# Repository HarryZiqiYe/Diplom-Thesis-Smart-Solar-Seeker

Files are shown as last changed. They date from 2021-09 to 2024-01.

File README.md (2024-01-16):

# Smart-Solar-Seeker

### Abstract

The paper hand in deals with the tracking of the sun, which follows the position of the sun, to get the maximum efficiency. Solar technology is a renewable energy source, that contributes to a sustainable environment. In contrast to flat lying solar panels, it is possible to produce more energy through tracking. A prototype has been developed and constructed which performs mostly all our tasks that we need.

Most of the mechanical components are standard aluminum profiles which are mainly used for the framework of our system, which can withstand weather and physical influences.
Furthermore, the project covers the implementation of a control algorithm on a microcontroller.
An GPS unit and light sensors have been used, which represents the input data of our algorithm. Two actuators, which have been installed, are controlled by the algorithm which are supposed to bring the solar panel to the the best solar radiation. The group compares with the measurements taken how economical it is to track and if it is necessary to rotate on two axes. An ESP32 microcontroller is used in the project and programmed with C++. Some circuit boards have been designed and implanted for our regulation of the supply voltage and for control of actuators, which uses inductors, relays, resistors, and other specific electronical components.

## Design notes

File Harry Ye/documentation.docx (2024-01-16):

# Photovoltaik: Stromerzeugung durch Sonnenenergie

Die Photovoltaik ist ein Prozess, bei der die Lichtenergie mit Hilfe von Solarzellen direkt in elektrische Energie umgewandelt wird. Diese Form der Energieerzeugung zählt zu den erneuerbaren.

# 1.1. Photoelektrischer Effekt

Unter den photoelektrischen Effekt (Photoeffekt oder lichtelektrischen Effekt) versteht man die Wechselwirkung der Elektronen mit den Photonen des Lichtes. Dabei nehmen die Elektronen die Photonen auf besser gesagt ihre Energie und lösen sich aus der Bindung des jeweiligen Stoffes. Diese Energie kann mit der Formel

| E=h∙f | (1.1)

E…Energie

h…Planck’sches Wirkungsquantum

f…Frequenz

berechnen. Um sich herauslösen zu können, muss die Photonenenergie größer als die Bindungsenergie des Elektrons sein. Es gibt drei Arten des photoelektrischen Effekts: äußeren, inneren und Photoionisation, wobei auf den inneren photoelektrischen Effekt genauer eingegangen wird.[1]

# 1.1.1. Äußerer photoelektrischer Effekt

Dieser Effekt wird auch als Photoemission oder Hallwachs-Effekt bezeichnet. Er beschreibt das Herauslösen der Elektronen aus einem Halbleiter- oder Metalloberfläche, wenn sie mit Licht bestrahlt wird. Dazu muss die Photonenenergie größer als die Austrittsarbeit des Materials sein. Mit der Gegenfeldmethode kann der Effekt demonstriert und die Austrittsarbeit bestimmt werden.

Abbildung 1.1 veranschaulicht dieses Phänomen.[2]

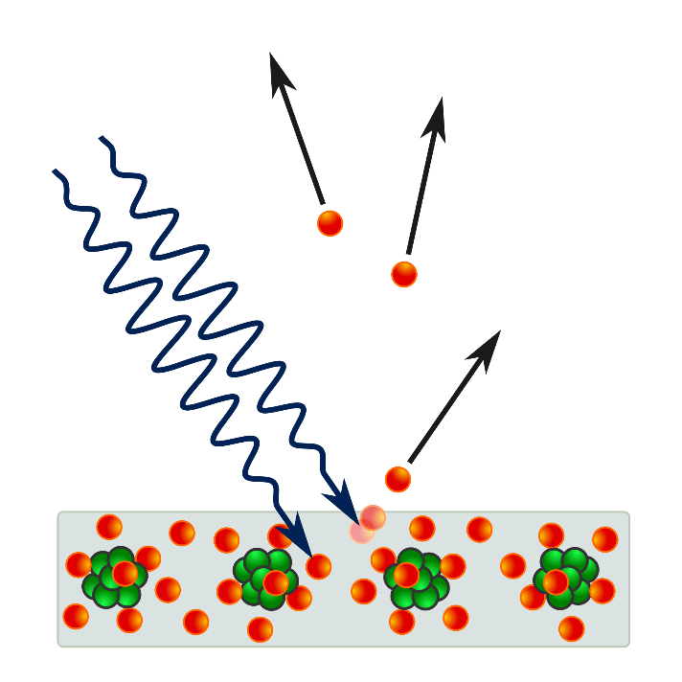
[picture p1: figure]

Abbildung 1.1: Äußerer photoelektrischer Effekt

# 1.1.2. Innerer photoelektrischer Effekt

Dieser Effekt tritt ausschließlich in Halbleiter auf. Zwei Fälle beschreiben diesen Effekt: Photoleitung und photovoltaischer Effekt.

# 1.1.2.1. Photoleitung

Wenn durch die Lichtbestrahlung die Leitfähigkeit eine Halbmaterials erhöht wird, spricht man von der Photoleitung. Um diesen Effekt besser verstehen zu können, ist das Bändermodell (Abbildung 1.2) abgebildet.

Abbildung 1.2: Bändermodell

Aufgrund der aufgebrachten Photonenenergie werden die Elektronen vom Valenzband in das Leitungsband gehoben. Die Photonen müssen so viel Energie aufbringen, bis die Elektronen die Bandlücke bzw. verbotenen Zone überwinden können. Während dieses Prozesses hinterlässt das Elektron ein Loch im Valenzband. So kommt es zur Bildung eines Elektronen-Loch Paars. Das Elektron im Leitungsband ist nun frei beweglich.[3]

# 1.1.2.2. Photovoltaischer Effekt

Durch das Prinzip der Photoleitung kann mit einem Halbleiter Licht in elektrische Energie umgewandelt werden. Dazu wird die Funktion einer Diode und seiner Raumladungszone gebraucht. Die Photonen brechen die Elektronenpaarbindungen auf. Wenn ein Verbraucher angeschlossen wird, ziehen sich die freibeweglichen Teilchen an und ein Strom beginnt zu fließen. Abbildung 1.3 stellt den Aufbau und die Funktion einer Solarzelle dar.[4]

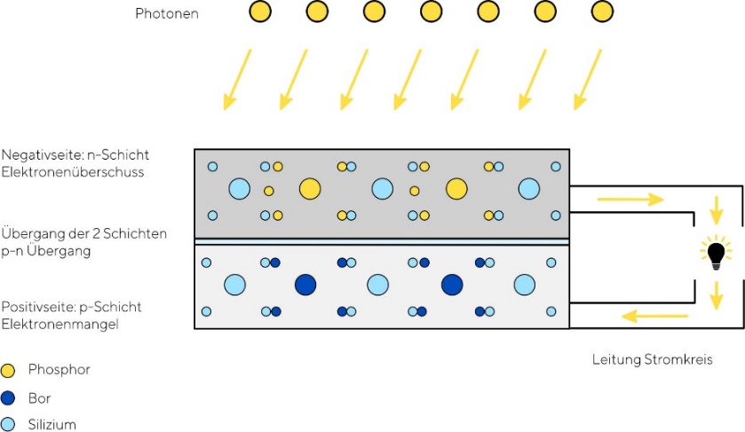
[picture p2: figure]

Abbildung 1.3: Solarzelle

# 1.2. Silizium-Solarzelle

Eine Solarzelle wandelt auf Grund des photovoltaischen Effektes Sonnenlicht in elektrische Energie um. Sie besteht aus einem Halbleitermaterial, wie Galliumarsenid, Cadmiumtellurid oder Chalkopyrite. Jedoch ist Silizium das häufigste verwendete Halbleitermaterial, weil es in großen Mengen zur Verfügung steht. Silizium-Solarzellen unterscheiden sich in zwei Arten: dickschichtig und dünnschichtig. Zu den Dickschichtzellen zählen die monokristallinen und polykristallinen Zellen und die amorphe Zelle gehört zu den Dünnschichtzellen.

# 1.2.1. Herstellung

Als Erstes wird aus Quarzsand Silizium gewonnen. Das Silizium wird zu Ingots verarbeitet. Danach werden die Ingots durch das Sägen zu Wafer. Die Wafer werden zu Solarzellen verbaut. (Abbildung 1.4)

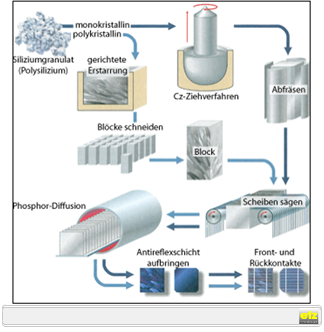
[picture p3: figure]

Abbildung 1.4: Herstellung

# 1.2.2. Verschiedene Typen von Solarzellen

Monokristallin: Solche Solarzellen bestehen aus einkristallinem Silizium, weshalb der Siliziumanteil sehr hoch ist. Der Wirkungsgrad einer monokristalline Zelle liegt bei ca. 20%. Sie ist vergleichsweise teurer als die anderen wegen der aufwendigeren Produktion.

Polykristallin: Bei den polykristalline Zellen ist das Silizium nicht so rein. Dadurch ist die Produktion weniger aufwendig und der Preis ist billiger, weshalb polykristalline Zellen das beste Preis-Leistung-Verhältnis haben. Der Wirkungsgrad liegt bei 15%.

Amorph: Dünnschichtzellen sind nichtkristallin. Das heißt, dass das Silizium mit anderen Materialien vermischt wird und auf eine dünne Schicht aufgetragen wird. Deshalb ist der Wirkungsgrad nur zwischen 5-7%. Jedoch sind sie flexibel und lassen sich falten und rollen. Die Zellen sind günstiger als Dickschichtzellen.[5]

# 1.2.3. Technische Merkmale

# 1.2.3.1. Kenngrößen

In den üblichen Technischen Datenblätter stehen folgende Kennwerte:

- ISC: Kurzschlussstrom
- VOC: Leerlaufspannung
- VMPP: Spannung bei maximaler Leistung
- IMPP: Strom bei maximaler Leistung
- PMPP: Maximale erzielbare Leistung unter STC
- FF: Füllfaktor

Der Füllfaktor ist ein Verhältnis zwischen der Leistung PMPP (Blau) und dem Produkt von ISC und VOC (Gelb) und dementsprechend dimensionslos. Sie gibt die Qualität der Zelle an. Für einen höheren Wirkungsgrad muss der Füllfaktor auch höher sein.

Abbildung 1.5: Füllfaktor

Den Füllfaktor berechnet man sich mit dieser Formel:

| FF=(P_(MPP))/(U_(OC) ∙I_(SC)) | (1.2)

PMPP … maximale Leistung

UOC … Leerlaufspannung

ISC … Kurzschlussstrom

TK PMPP: Koeffizient für die Leistungsänderung abhängig von der Zellentemperatur.

η: Zellwirkungsgrad

| η=(P_(MPP))/(A∙E_e) | (1.3)

A … bestrahlte Fläche

Ee … Bestrahlungsstärke

Aus den Kennwerten kann eine Strom-Spannungs-Kennlinie erstellt werden (Abbildung 1.6).[6]

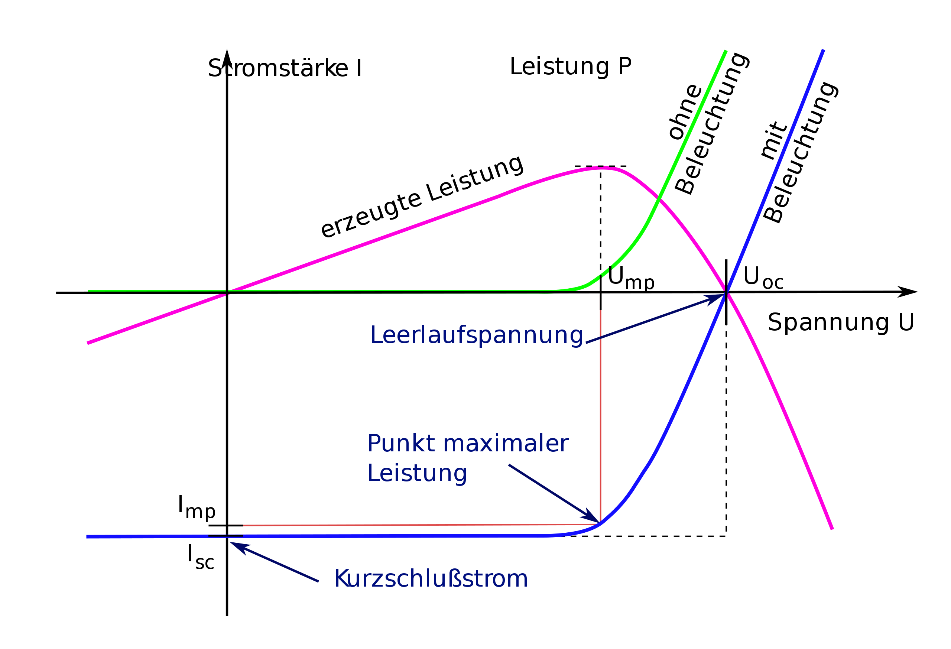
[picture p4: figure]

Abbildung 1.6: Strom-Spannungs-Kennlinie

# 1.2.3.2. Schaltbilder

Das Schaltsymbol einer Solarzelle (Abbildung 1.7).

Abbildung 1.7: Schaltsymbol

Ein Ersatzschaltbild schaut folgendermaßen aus (Abbildung 1.8):

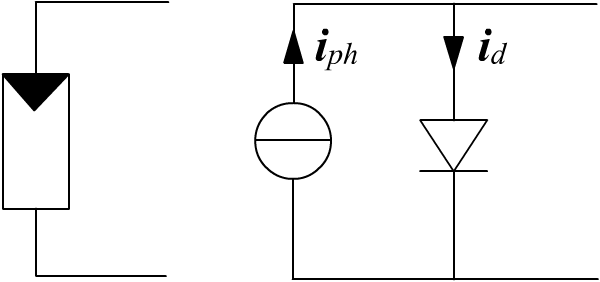
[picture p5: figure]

Abbildung 1.8: Ersatzschaltbild

Links ist das Schaltzeichen einer Solarzelle und Rechts abgebildet ihr Ersatzschaltbild. Die Gesamtstromstärke wird errechnet mit:[7]

| I=I_(ph) -I_D | (1.4)

# 1.2.4. Solarpanel

Einzelne Solarzellen werden in Reihe bzw. in Serie geschalten (Abbildung 1.9). Dadurch entsteht ein Solarpanel oder Solarmodul. Die Spannungen der jeweiligen Solarzelle werden zusammenaddiert. Werden die Solarzellen parallel geschalten, so werden die Ströme addiert (1.10).

Abbildung 1.9: Reihenschaltung

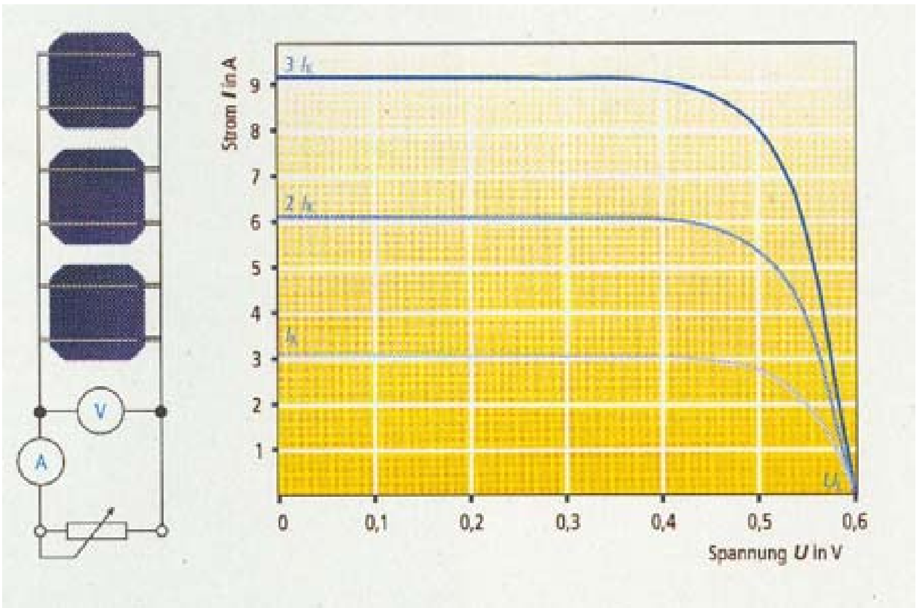
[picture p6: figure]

Abbildung 1.10: Parallelschaltung

Häufig befinden sich Bypass-Dioden bzw. Freilaufdioden in den Solarmodulen. Abbildung 1.11 zeigt eine abgeschattete Solarzelle in einer Reihenschaltung.

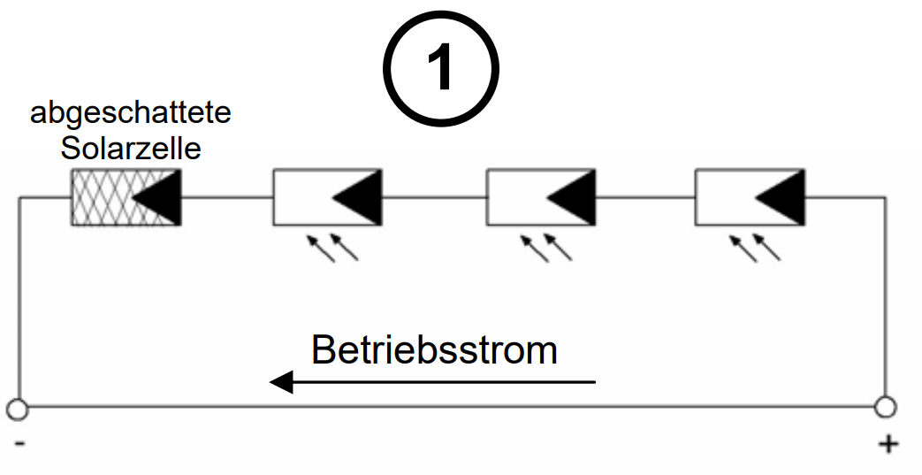
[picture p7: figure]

Abbildung 1.11: abgeschattete Solarzelle

Diese abgeschattete Zelle wirkt wie ein Widerstand bzw. Verbraucher. Der durchfließende Strom wandelt sich in Wärme um und die Solarzelle überhitzt sich. Das wird Hotspot genannt (Abbildung 1.12).

Abbildung 1.12: Hotspot

Wird nun eine Freilaufdiode antiparallel geschaltet, entsteht ein Kurzschluss und die Diode leitet den Strom um (Abbildung 1.13).

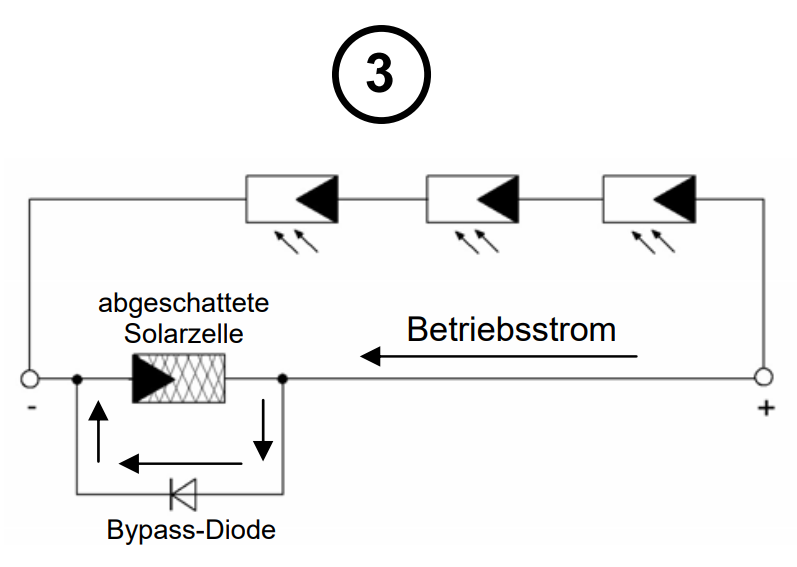
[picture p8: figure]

Abbildung 1.13: Bypass-Diode

In der Praxis wird nur eine Bypass-Diode pro Solarmodul verbaut. Das heißt ist ein Solarmodul beschattet, so leitet die Diode den Strom um (Abbildung 1.14).[8]

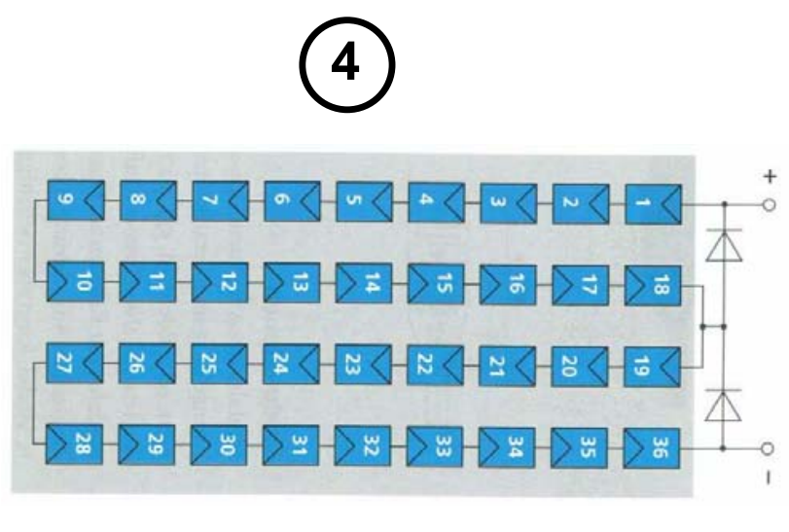
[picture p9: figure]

Abbildung 1.14: eine Bypass-Diode pro Solarmodul

In unserem Projekt wird ein monokristallines Solarpanel verwendet. Technische Daten:

- Nennleistung Pmax: 90W mit einer Toleranz von 5%
- Strom bei Pmax Imp: 5,25A
- Spannung bei Pmax Vmp: 17,98V
- Kurschlussstrom ISC: 5,65A
- Leerlaufspannung VOC: 22,77V
- Gewicht: 7,8kg
- Abmessungen: 1185x545x35mm

# 1.2.5. Wirkungsgrad

Der Wirkungsgrad ist das Verhältnis der Ausgangsgröße und die Eingangsgröße. Beim Leistungsverhältnis einer Solarzelle ist es die erzeugte elektrische Leistung durch die einfallende Strahlung:

| η=(P_(elektrisch))/(P_(Licht)) | (1.5)

η … Wirkungsgrad

Pelektrisch … erzeugte elektrische Leistung

PLicht … einfallende Strahlungsleistung

Wirkungsgrade der verschiedenen Zellarten:

Material | Max. Wirkungsgrad im Labor | Max. Wirkungsgrad Serienproduktion | Typ. Wirkungsgrad Serienproduktion | Flächenbedarf pro kW
Monokristallin | 26,1% | 24% | 19% | 5,3m²
Polykristallin | 22,3% | 20% | 17% | 5,9m²
Amorph | 14% | 8% | 6% | 16,7m²

Der Wirkungsgrad der Solarzellen wird mit den Standard-Test-Conditions gemessen (1000 Watt Lichteinstrahlung, 25 Grad Zelltemperatur, Air Mass von 1,5).

Um den Wirkungsgrad einer Solarzelle technisch zu verbessern, muss das Material mehr Lichtwellen des Spektrums verarbeiten können. Tandem-Solarzellen bestehen aus verschiedenen Stapeln von Materialien, somit wird ein breiteres Spektrum abgedeckt.[9]

Eine Solarzelle kann auch Wirkungsgrad verlieren. Wenn die Zelltemperatur zu hoch ist, verliert die Zelle an Wirkungsgrad, weil sie weniger Leistung erzeugt. In der Regel nach den STCs sinkt die Leistung um 0,4% pro Grad Celsius. Außerdem haben Solarzellen eine bestimmte Lebensdauer. Bei kristallinen Zellen liegen sie über 30 Jahren und bei amorphen 20 bis 25 Jahren. Von Jahr zu Jahr verringert sich der Wirkungsgrad einer Solarzelle.[10]

# 1.3. Azimut und Elevation

Azimut und Elevation sind Maße, die die Koordinaten eines Objektes in der Atmosphäre beschreibt. Die Richtung gibt der Azimut an und die Höhe die Elevation. Beide werden in Grad angegeben. Abbildung 1.15 zeigt einen Satellit und seiner Elevation und seines Azimuts. Auch der Standort der Sonne kann mit den beiden Größen bestimmt werden.

Abbildung 1.15: Azimut und Elevation

Der Winkel zwischen Meridian und des Satelliten ist der Azimut. Von Norden im Uhrzeigersinn wird gemessen. Eine volle Umdrehung ist 360°.

Der Winkel zwischen dem Horizont und des Mittelpunktes wird Elevation genannt. Im Zenit ist der maximale Elevationswinkel 90°.[11]

# Regelungsentwickelung

# 1.4. Recherche und Vorwissen

Regeln ist das selbsttätige Beeinflussen eines technischen Prozesses (einer Anlage, eines Systems) in gezielter Weise. Dabei handelt es sich um einen geschlossenen Wirkungsablauf; das heißt, die den Prozess beeinflussenden Größen werden mit geeigneten Regeleinrichtungen aus gemessenen Prozessgrößen selbst gebildet und nicht nur von außen vorgegeben.[^1]

Abbildung 2.1 veranschaulicht die Regelung einer antiken Wasseruhr.

Abbildung 2.1: Antike Wasseruhr

Bei einer bestimmten Füllhöhe h des Wassers sind der Zufluss und Abfluss gleichgroß ( q_z =q_a ), weil der Schwimmer den Zufluss bei steigender Wasserhöhe verringert.[12]

# 1.4.1. Darstellung eines Regelungssystems

Ein Geräteplan stellt schematisch die gerätemäßige Realisierung einer Regelung dar (Abbildung 2.2).

Abbildung 2.2: Geräteplan

Die Drehzahl des Motors wird gemessen. Anhand des Istwertes wird eine entsprechende Steuerspannung in den Stromrichter geschickt, um den Sollwert anzunähern.

Ein Blockschaltbild stellt die Regelung in Funktionsblöcken dar. Dabei werden die einzelnen Funktionen der Geräte vereinfacht. Abbildung 2.3 zeigt die obige Drehzahlregelung als vereinfachtes Blockschaltbild an.[12]

Abbildung 2.3: Blockschaltbild

# 1.4.2. Regelkreis

Die Abbildung 2.3 zeigt den Aufbau eines Regelkreises. Allgemein schaut der Regelkreis so aus:

Abbildung 2.4: Regelkreis

Elemente:

- Regler: Der Regler versucht die Regelabweichung (Differenz zwischen Sollwert und Istwert) zu eliminieren bzw. auf null zu setzen. Dafür erzeugt er ein entsprechendes Signal.
- Stellglied: Dieses Signal nimmt das Stellglied (z.B. Verstärker, Stromrichter, Servomotor, Ventil) auf. Da das Signal des Reglers eine leistungsschwache Größe ist und die Regelstrecke meist eine leistungsstarke Größe benötigt, dafür wird ein Stellglied eingesetzt, das so eine Stellgröße ausgeben kann.
- Regelstrecke: Die Regelstrecke ist das System, das geregelt wird. Sie gibt die Regelgröße bzw. den Istwert aus.
- Messglied: Das Messglied misst den jetzigen Istwert. Dieser Istwert wird in eine für den Regler verwendbare Größe umgeformt.
- Störgröße: Da Störungen unvermeidlich sind, müssen sie so weit minimalisiert werden, bis sie irrelevant sind. Sie treten während der Regelung der Strecke auf.

Sehr oft wird der Regler und das Stellglied als einen Block zusammengefasst. Das gilt auch für die Regelstrecke und das Messglied. Daraus ergibt sich der Standardregelkreis (Abbildung 2.5):[12]

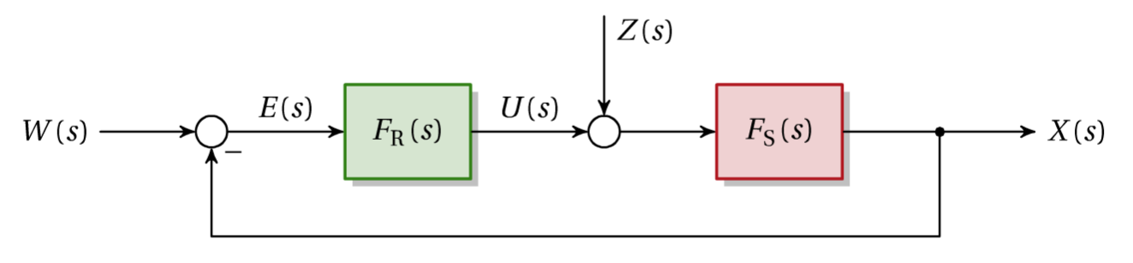
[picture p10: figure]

Abbildung 2.5: Standardregelkreis

Die wichtigsten Größen sind:

- X(s) … Regelgröße (Istwert)
- W(s) … Führungsgröße (Sollwert)
- E(s) … Regelabweichung
- U(s) … Stellgröße
- Z(s) … Störgröße
- FR(s) … Übertragungsfunktion des Reglers
- FS(s) … Übertragungsfunktion der Regelstrecke

Ohne der Rückführung im Regelkreis erhält man den offenen Regelkreis, mit der Übertragungsfunktion FO:[12]

| F_O (s)=F_R (s)∙F_S (s) | (2.1)

Schließt man den Regelkreises, bekommt man die Führungsübertragungsfunktion FW:

| F_W =(F_R ∙F_S)/(1+F_R ∙F_S)=(F_O)/(1+F_O) | (2.2)

# 1.4.3. Regler

Der Regler hat die Aufgabe, die Führungsgröße (Sollwert) mit der Regelgröße (Istwert) zu vergleichen und aus der Differenz beider Größen (Regelabweichung) eine entsprechende Stellgröße zu erzeugen.[^2] Zwischen den elektrischen Reglern unterscheidet man analoge und digitale.[12]

Es gibt drei Grundtypen der analogen Regler:

- P-Regler: Erzeugt eine der Regelabweichung proportionale Stellgröße. Vorteil: Schnelles Reagieren auf Regelabweichung, Nachteil: Regelt nie komplett aus (Ausnahme: Regelstrecke mit I-Anteil)
- I-Regler: Erzeugt eine Stellgröße, die dem zeitlichen Integral der Regelabweichung proportional ist. Vorteil: Genaue Regelung der Abweichung, Nachteil: Langsames Reagieren auf Regelabweichungen
- D-Regler: Erzeugt eine Stellgröße, die der momentane Änderungsrate der Regelabweichung proportional ist. Vorteil: Verbessert das Stabilitätsverhalten des Regelkreises, Nachteil: Regelt nicht aus → nur mit anderen Reglern sinnvoll

Durch Parallelschalten der einzelnen Grundregler erhält man:

- PI-Regler
- PD-Regler
- PID-Regler

Die Aspekte der einzelnen Regler werden kombiniert. Abbildung 2.6 veranschaulicht die Funktionen der Regler (Stellgrößen bei gegebener Regelabweichung):[12]

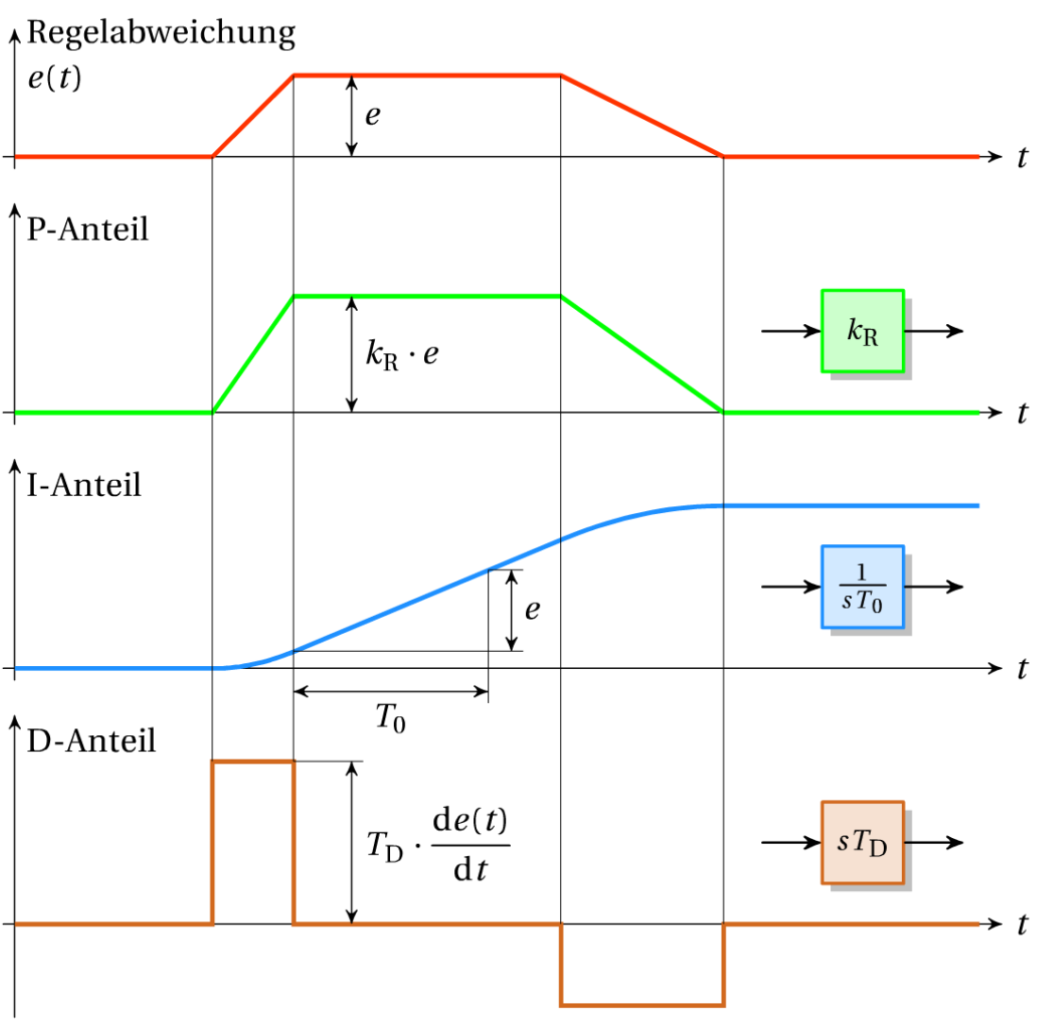
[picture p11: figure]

Abbildung 2.6: Erzeugte Stellgröße

Verglichen zu analoge Regler, die aus elektronische Bauteile (z.B. OPV) bestehen, werden für digitale Regler Computer (z.B. Mikrocontroller) verwendet. Die Regelgröße wird in periodischen Zeitabständen von einem Analog-Digital-Converter kurz ADC in eine digitale Größe konvertiert und vom Rechner eingelesen. Die Führungsgröße wird im Programm eingegeben oder von außen durch einen ADC hineingeschickt.[12]

Abbildung 2.7: Digitaler Regler

Im gespeicherten Programm des Computers arbeitet ein Regelalgorithmus Schritte ab, um die Stellgröße mit der berechneten Regelabweichung zu erhalten. Die Stellgröße kann entweder wieder in ein analoges Signal umgewandelt werden oder durch ein PWM-Signal gesendet werden.

Ein Digital-Analog-Converter wandelt digitale Signal in analoge um. Abbildung 2.8 veranschaulicht die analoge Umwandelung der Stellgröße.[12]

Abbildung 2.8: Analoge Umwandelung

Pro Zeitabstand wird die Stellgröße einmal abgetastet und bis zur nächsten Abtastung wird der Wert konstant gehalten.

Das pulsbreitenmodulierte Signal PWM stellt die Stellgröße als Rechtecksignal mit einer bestimmten Frequenz dar. Das Verhältnis zwischen der Impulsdauer und der Periodendauer, auch Duty-Cycle genannt, ermöglicht das Erzeugen eines bestimmten Stellgrößenwertes (Abbildung 2.9).

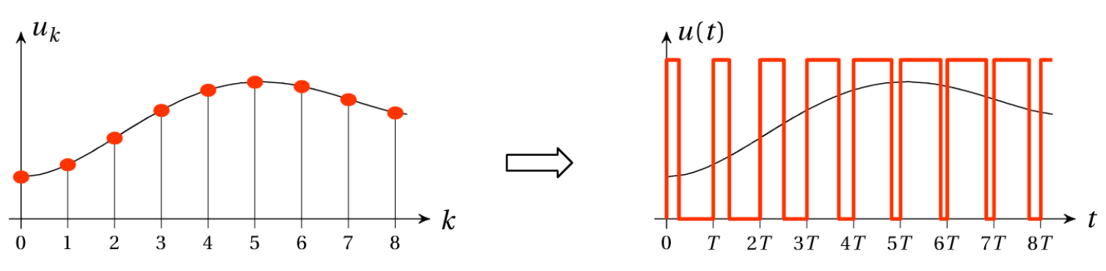
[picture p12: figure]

Abbildung 2.9: PWM

Da die Erzeugung des PWM-Signals rein softwaretechnisch verläuft, ist ein DAC nicht essenziell.[12]

# 1.4.4. Theoretischer Ansatz

Das Solarpanel wird zwei-achsig nachgeregelt. Ein Motor für die Azimut-Achse und ein anderes für die Elevation. Dabei wird zwischen Osten und Westen geregelt und danach der Höhenwinkel eingestellt. Nach der ersten Regelung wird jede Stunde wieder nachgeregelt. Bei schlechtem Wetter wie bei Bewölkung wird nicht nachgeregelt. Am Anfang der Regelung muss ein Nullpunkt definiert werden, damit das Programm richtig funktioniert.

# 1.4.5. Praktischer Ansatz

Abbildung 2.10 zeigt den entworfenen Regelkreis.

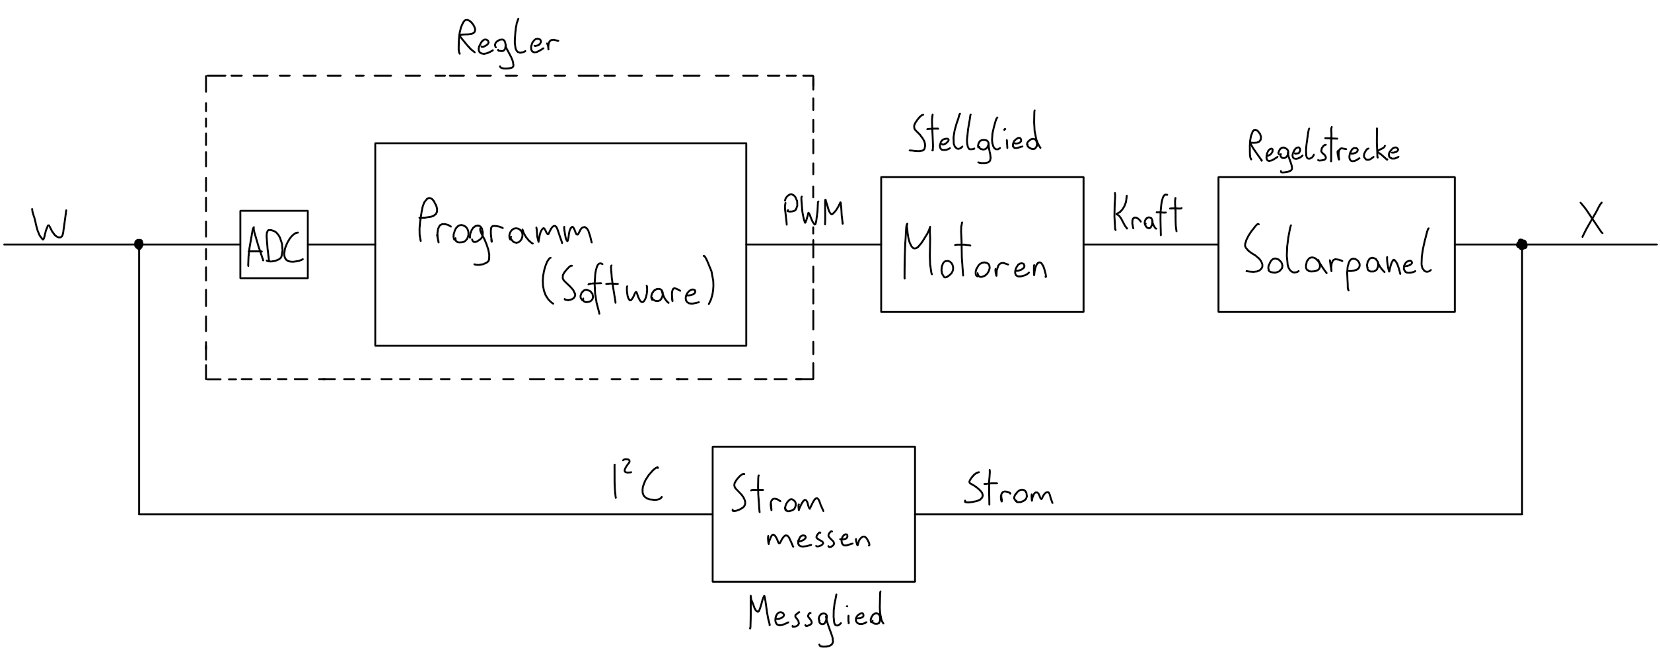
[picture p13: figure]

Abbildung 2.10: Theoretischer Ansatz

Für den digitalen Regler wird ein ESP32 verwendet, der alle benötigten Funktionen (Eingebauter ADC, I²C-Schnittstelle, das Erzeugen von PWM-Signalen, usw.) abdeckt (Regler). Das Bewegen des Azimuts beim Solarpanel erledigt ein Schrittmotor und beim Höhenwinkel ein Linearmotor (Stellglied). Im Gegensatz zum großem Solarpanel wird ein kleineres zur Messung des Stroms genommen (Regelstrecke). Das Messen übernimmt ein Stromsensor, der den Stromwert in digitale Spannungsimpulsen umwandelt und über die I²C-Schnittstelle zum Mikrokontroller schickt (Messglied). Im Folgenden werden die für die Regelung verwendeten Komponenten beschrieben.

# 1.5. Stromsensor

Der Stromsensor soll den Strom des kleineren Solarpanels messen und in eine digitale Größe umwandeln, damit der Mikrokontroller den Wert verarbeiten kann. Dabei werden zwischen zwei Arten unterschieden.

# 1.5.1. ACS712: Hall-Sensor

Die erste Variante der Strommessung ist mit einem Hallsensor. Er misst den Strom auf Basis des Halleffekts und wandelt ihn Spannung um. (Abbildung 2.11)

Abbildung 2.11: ACS712

# 1.5.1.1. Halleffekt

Wird ein stromdurchflossener Leiter in der Nähe eines Dauermagnets platziert, so bewegen sich die Ladungsträger senkrecht zum Magnetfeld des Dauermagnets, wodurch sich die geradlinigen Bahnen des Leiters krümmen. Es wirkt eine Lorentzkraft auf den Ladungsträger. Nun sind mehr Ladungsträger auf einer Seite im Leiter. Dadurch entsteht ein Potenzialunterschied, die Hallspannung. Diese Spannung ist abhängig von der Distanz des Magneten zum Leiter. Bei einem digitalen Hallsensor muss der Magnet in einer gewissen Reichweite sein, damit sich das Ausgangssignal ändert (Abbildung 2.12).[16]

Abbildung 2.12: Halleffekt

Die ACS712 Module liefern max. 185 Millivolt pro Ampere. Aus diesem Grund ist der ACS712 ungeeignet für die Regelung, weil das Miniaturpanel zu wenig Strom liefert, um eine genügend große Ausgangsspannung zu erzeugen. Die maximale Anzahl der Schritte des ADCs bei einem Maximalstrom von 340mA kann mit Rechnungen ermittelt werden:

| V_(maxACS712) =Sensitivität des ACS712∙A_(maxPanel) =(185mV)/A∙0,34A=62,9mV | (2.3)

VmaxACS712 … Max. Ausgansspannung des ACS712

AmaxPanel … Max. Strom des kleinen Panels

| ADC_(V pro Schritt) =(Referenzspannung des ADCs)/(Auflösung des ADCs)=(3,3V)/(2^12 counts)=0,806mV/count | (2.4)

Aus der ersten Rechnung erhält man die maximale Ausgangspannung des Moduls und aus der zweiten die Spannung pro Schritt des AD-Wandlers des ESP32. Werden die beiden Werte dividiert,

| max. Schritte=(V_(maxACS712))/(ADC_(V pro Schritt))=(62,9mV)/(0,806mV/count)=78,75 counts | (2.5)

erhält man 78 Schritte, die der ESP32 darstellen kann. Das heißt, dass der Unterschied zwischen einen Milliampere nicht festgestellt werden kann. Der Sensor ist für größere Ströme geeignet.

# 1.5.2. INA219: Shuntwiderstand

Durch das Ohm’sche Gesetz kann mit einem Shuntwiderstand Strom gemessen werden.

# 1.5.2.1. Shuntwiderstand

Shuntwiderstände werden zur Messbereichserweiterung eines Amperemeters eingesetzt. Dabei wird der Widerstand parallel zum Amperemeter geschaltet (Abbildung 2.13).

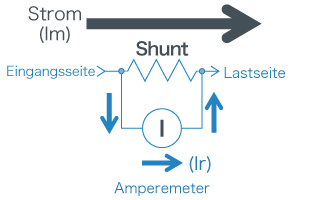
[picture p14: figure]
Shunt Widerstand [Stromteiler]

Abbildung 2.13: Shuntwiderstand

Durch das Amperemeter mit einem Innenwiderstand r fließt ein Strom Ir. Der Gesamtstrom Im fließt durch das Amperemeter und dem Shuntwiderstand R. Daraus ergibt sich eine Formel:

| I_m =I_r ∙(1+r/R) | (2.6)

Somit kann der Strom Im, der den Messbereich übersteigt, gemessen werden.

Außerdem wird ein Shuntwiderstand zur Messung von Strömen verwendet. In dem der Spannungsabfall am Widerstand gemessen wird und der Strom mit dem ohmschen Gesetz berechnet wird.[17]

Der INA219 ist ein Bauteil, der die Spannung am Shuntwiderstand misst. Die schematische Darstellung Abbildung 2.14 zeigt den Aufbau des INA219s.

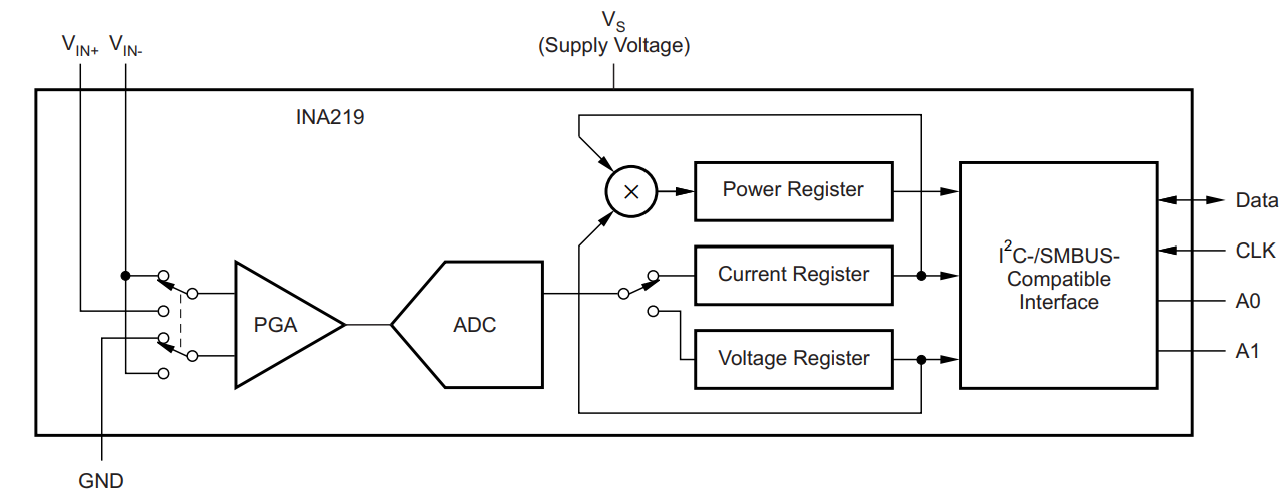
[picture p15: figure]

Abbildung 2.14: Schematic INA219

Die Shunt-Spannung, die am VIN+ und VIN- angelegt wird, wird vom PGA Programmable Gain Amplifier verstärkt. Dabei ist es egal, ob die Potentiale vertauscht angelegt werden, denn der INA219 setzt nur ein negatives Vorzeichen vor dem ausgegebenen Wert. Die Versorgung soll im Bereich von 0 bis 26V sein und bei 0,1Ω sollte der Strom maximal 3,2A sein. Der INA219 selbst muss mindestens mit 3V und höchstens 5,5V versorgt werden.

Abbildung 2.15: INA219 Spannungen

Wie im Name schon steht, kann der PGA programmiert werden. Dabei gibt es vier mögliche Bereiche, die eingestellt werden können. Die Zahl steht für die maximale Shunt-Spannung in mV, die bei diesem Bereich anliegen darf:

- PG_320
- PG_160
- PG_80
- PG_40

Je niedriger der Bereich, desto genauer bzw. höher ist die Auflösung.

Nach der Verstärkung wandelt der ADC die analogen Signale in digitale um und speichert sie ins jeweilige Register hinein. Auch die Auflösung des ADCs kann geändert werden. Es kann zwischen 9 bis 12 Bit ausgewählt werden. Hier gilt je größer die Auflösung desto länger dauert die Umwandlungszeit. Zum Vergleich: Bei einem 9 Bit dauert es 84µs und bei 12 Bit 532µs. Auch können mehr Proben (Samples) pro Messung eingestellt werden. Der Durchschnitt der Samples ist der tatsächliche Wert. Vorteil ist, dass starke Messabweichung geringe Auswirkung auf den Endwert hat. Nachteil ist die längere Conversion-Time. Bei 12 Bit Auflösung mit 2 Samples dauert es 1,06ms, somit das doppelte zur vorherigen Zeit. Die Zeit und Samples sind direkt proportional zueinander und verdoppeln sich pro Schritt. Das heißt, dass bei 128 Samples die Totzeit bei 68,1ms liegt.

Die umgewandelte Werte vom ADC werden in den jeweiligen Register gespeichert. Der Power Register speichert die Leistung aus der Multiplikation vom Current- und Voltage-Register. Auf Anforderung vom Mikrokontroller werden die gespeicherten Werte abgerufen und per I²C-Schnittstelle transportiert.

Im Datenblatt ist der Schritt pro V vom 12 Bit ADC mit einem PG_40 angegeben. LSB-Schrittgröße ist 10 µV. Die Schrittanzahl der maximalen Shunt-Spannung ist:

| max. U_(Shunt) =max. I_(Shunt) ∙R_(Shunt) =0,34A∙0,1Ω=34mV | (2.7)

max. UShunt … maximale Shunt-Spannung

max. IShunt … maximaler Shunt-Strom

RShunt … Shuntwiderstand

| max. Schritte=(max. U_(Shunt))/(ADC_(V pro Schritt))=(34mV)/(10µV/count)=3400 counts | (2.8)

Verglichen zum ACS712 sind die Counts wesentlich höher und Änderungen der Werte in Mikrobereich werden erkannt.

Es können insgesamt vier Stromsensoren gleichzeitig im Betrieb genommen werden. Die Pins A0 und A1 am INA219 sind für die Änderung der Adresse zuständig. Sie können entweder auf HIGH oder LOW gelötet werden.

Der INA219 hat verschiedene Modi mit jeweiligen Funktionen.

- Kontinuierlich Modus: Misst den Wert andauernd. Auch ohne Anfragen vom µController werden die Register ständig mit neuen Werten aktualisiert.
- Triggered Modus: Es wird nur gemessen, wenn auch eine Anforderung verschickt wurde. Dabei werden alle Messungen auf einmal ausgegeben und gehören zu einem Messzyklus.
- Power-Down Modus: Im Normalbetrieb verbraucht der Sensor 0,7mA. Im Power-Down Modus nur 10µA. Mit einer Funktion kann der INA219 in den Stand-By gebracht werden.

Die Pin-Konfiguration des SOT-23 Gehäuses ist in der Abbildung 2.16 dargestellt.[18]

Abbildung 2.16: Pin-Konfiguration

Name | Pin | In/Out | Beschreibung
IN+ | 1 | Analog Input | Höheres Potential des Shunt-Widerstands
IN- | 2 | Analog Input | Niedriges Potential des Shunt-Widerstands
GND | 3 | Analog | Ground
VS | 4 | Analog | Versorgungsspannung (3 bis 5,5V)
SCL | 5 | Digital Input | Clock-Leitung der I²C-Schnittstelle
SDA | 6 | Digital I/O | Daten-Leitung der I²C-Schnittstelle
A0 | 7 | Digital Input | Adress-Pin der I²C-Schnittstelle
A1 | 8 | Digital Input | Adress-Pin der I²C-Schnittstelle

# 1.5.3. HW-831 Modul

Um den INA219 nutzen zu können, muss dafür ein Modul erstellt werden. Dafür wurde in KiCad ein Schaltungsplan und PCB entworfen (Abbildung 2.17 und Abbildung 2.18). Nur noch die Bauteile haben gefehlt. Leider war der INA219 auf RS-Components nicht verfügbar. Aus diesem Grund wurde ein fertiges HW-831 Modul von Amazon gekauft.

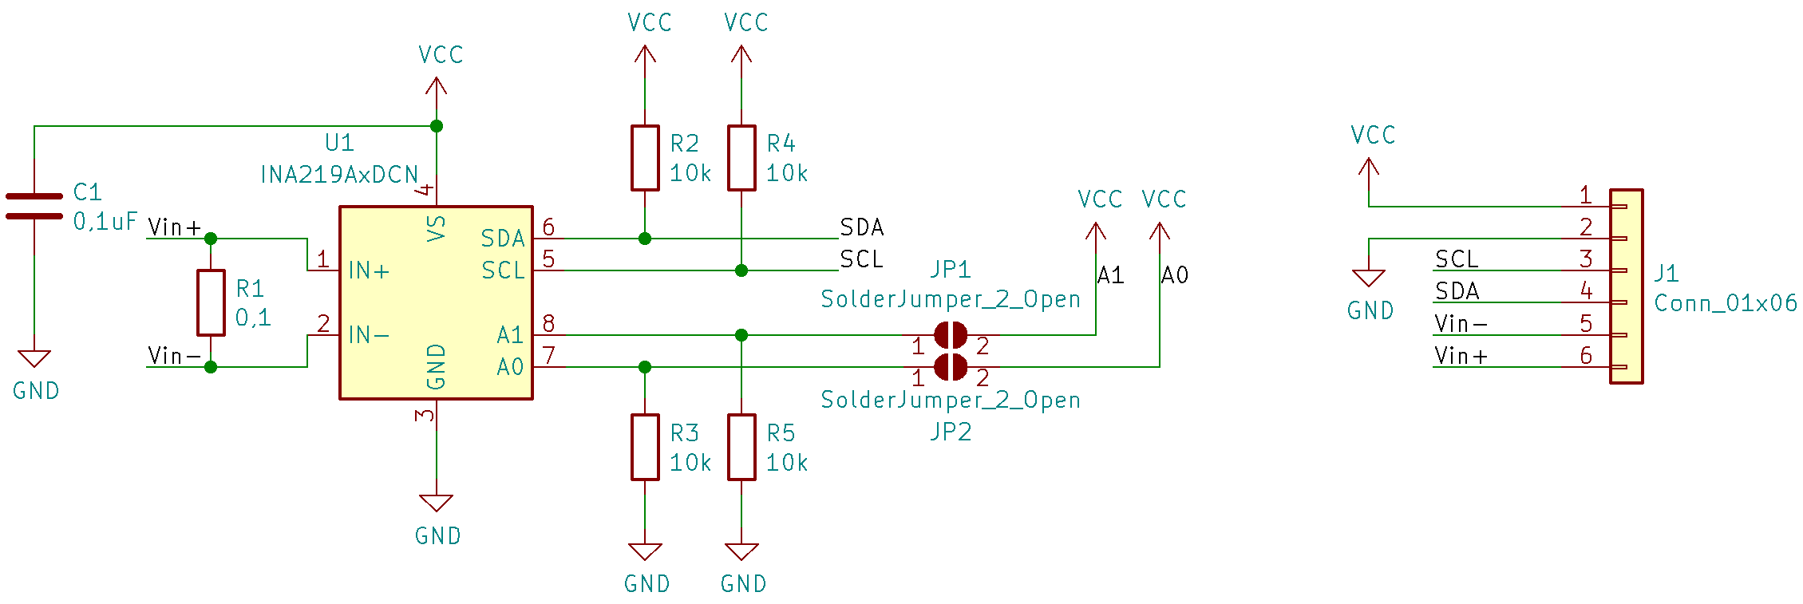
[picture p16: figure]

Abbildung 2.17: INA219 Schaltplan

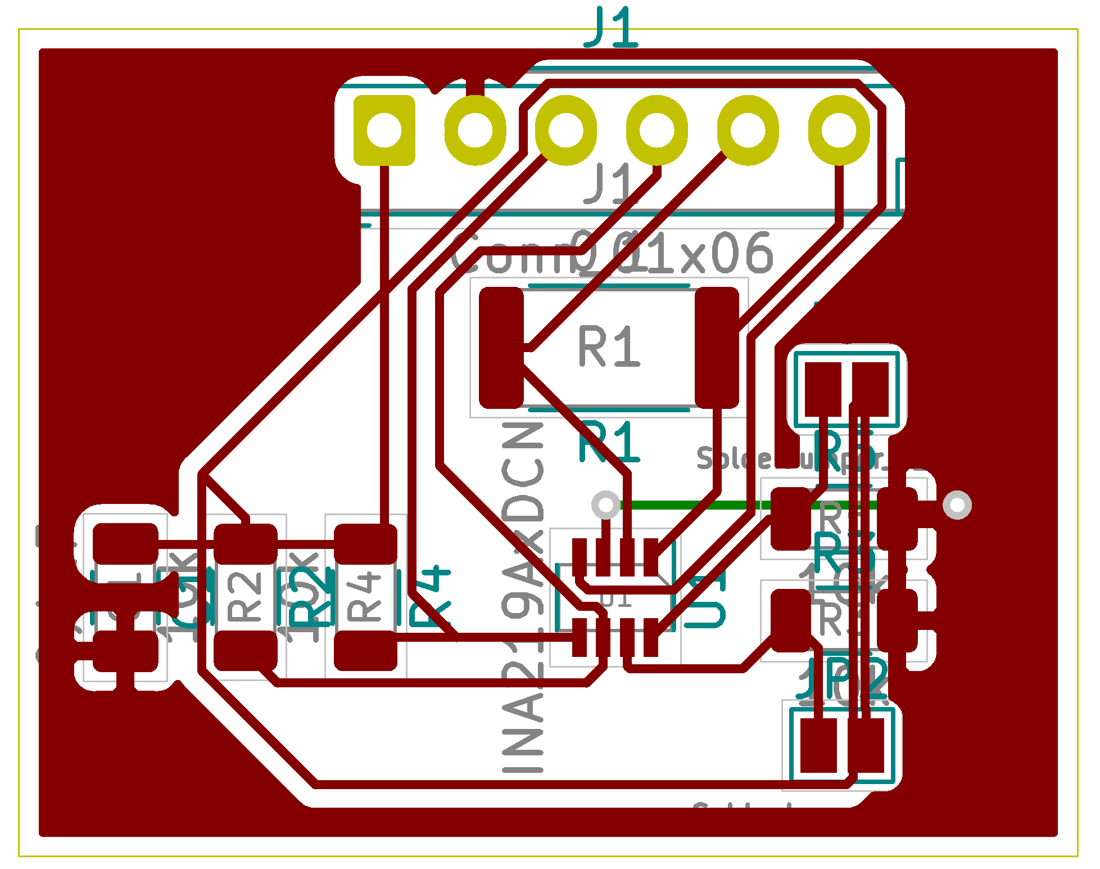
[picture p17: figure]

Abbildung 2.18: PCB Design

Die beiden Widerstände an den SCL und SDA Pins sind Pull-Up-Widerstände. Sie ziehen die Leitungen auf die Versorgungsspannung und sind somit auf HIGH-Level, da der Pin eine Open-Collector-Schnittstelle hat. Das heißt, dass der Pin ohne Pull-Up-Widerstände keinen exakten logischen Wert einnimmt, wenn es nicht gerade auf GND gezogen wird. Das kann zu Datenverlust führen. Der typische Wert eines Pull-Up-Widerstands liegt bei 10kΩ. Je niedriger der Widerstand, desto höher ist die Geschwindigkeit der Leitung. Bei höheren Werten ist der Leistungsverbrauch niedriger. Die Adress-Pins sind normalerweise auf GND, aber sie können auf VCC gelötet werden. Das ändert die logische 0 auf eine logische 1 im Register. Der Stützkondensator am VS-Pin stabilisiert die Versorgungspannung. Er wird parallel zur Versorgung geschalten. Die Zuleitung für Speisespannungen und GND zu den ICs sind parasitär induktiv. Das heißt, dass sehr schnelle Stromsteigerungen passieren können, die zu einer sehr schnelle Änderung der Speisespannung führt. Der Kondensator mindert den Stromimpuls, damit die Versorgung nicht einbricht.

Das Layout des HW-831 Moduls ist ein wenig anders, aber die Funktion ist dieselbe (Abbildung 2.19 und Abbildung 2.20).

Abbildung 2.19: Vorderansicht des Moduls

Abbildung 2.20: Hinteransicht des Moduls

# 1.6. Hallsensor

Ein Hallsensor wird benötigt, um ein Startposition auf der Azimut-Achse zu definieren. Der Halleffekt wurde bereits erklärt. Der gewählte Sensor ist der A1120 und ist ein digitaler Hallsensor (Abbildung 2.21).

Abbildung 2.21: Hallsensor A1120

Das heißt, dass er am Ausgang eine logisch 0 oder 1 ausgibt. Außerdem ist er unipolar. Wenn ein Magnet mit seiner Südpolseite den Hallsensor annähert, beginnt er sich zu aktivieren. Bei einem Bipolaren braucht es Nord- und Südpol für die Aktivierung. Der Südpol schaltet ihn ein und der Nordpol wieder aus. Der Sensor ist stationär, während das Magnet mit dem Solarpanel dreht. Das Magnet bzw. Solarpanel zeigt bei der Startposition nach Süden. Um Verschaltung zu vereinfachen, wurde ein Modul gemacht. Dabei wurden nur ein Pull-Up-Widerstand und eine Pin-Leiste hinzugefügt (Abbildung 2.22).

Abbildung 2.22: A1120 Modul

# 1.7. Regelungsimplementierung in die Software

Der digitale Regler ist ein ESP32. Mit der Arduino IDE kann der Mikrokontroller programmiert werden. Die Entwickelungsumgebung basiert auf die Programmiersprache C, eine prozedurale und imperative Sprache, das heißt, dass die Programmzeilen nach der Reihenfolge abgearbeitet werden. Ein Arduino-Programm besteht aus zwei Teilen: einem Setup und einem Loop. Im Setup werden alle Zeilen nur einmal ausgeführt und im Loop werden die Zeilen nach dem ersten Durchlauf immer wiederholt. Abbildung 2.23 zeigt den Zyklus des Regelalgorithmus:

Lohnt sich Regelung?
Azimut: Strommaximum suchen
Schrittmotor zum Maximum ansteuern
Höhenwinkel: Strommaximum suchen
Linearmotor zum Maximum ansteuern
Wenn Azimut 180° gedreht hat, wieder zurückdrehen

Abbildung 2.23: Grafische Darstellung des Algorithmus

Zuallererst stellt sich die Frage, ob sich die Reglung lohnt. Ist die Antwort ja, dann läuft das Programm weiter. Wenn das Gegenteil der Fall ist, bleibt das Programm stehen und misst weiterhin den Strom, bis er groß genug ist. Nach dieser Feststellung wird der Schrittmotor angesteuert und die Mechanik beginnt sich waagrecht zu drehen. Der Stromsensor liest pro Schritt, den der Schrittmotor zurücklegt, den Stromwert ein. Er dreht sich so lange weiter, bis ein gewisser Azimut-Winkel erreicht wurde. Danach dreht sich das Solarpanel zur Anfangsposition hin und von dort aus beginnt der Prozess von Neuem nur in die andere Richtung. Der Beginn der Regelung kann folgendermaßen veranschaulicht werden (Abbildung 2.24):

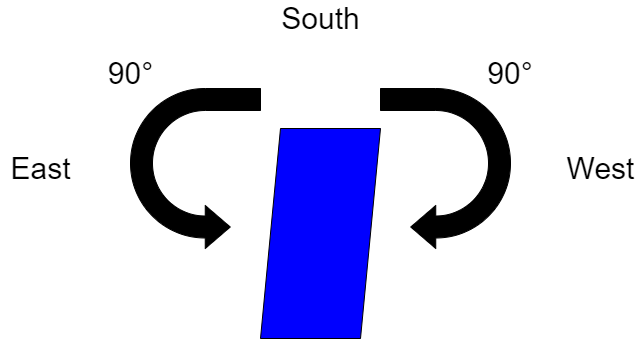
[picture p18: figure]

Abbildung 2.24: Beginn der Regelung

Das blaue Rechteck ist das Solarpanel und zeigt in der Nullpunktposition nach Süden. Danach dreht es sich um 90° nach Westen und sucht sich das Maximum. Dasselbe wird nach Osten gemacht. Nun werden die beiden Maxima verglichen. Anschließend dreht sich das Panel zum größeren Maximum. Nach einer Stunde hat sich die Sonne bereits weiterbewegt. Da die Änderung nicht allzu groß ist, werden nur ±15° zurückgelegt.

Die Elevation wird nach dem gleichen Prinzip geregelt. Die Nullpunktposition ist bei 90° Höhenwinkel, wenn der Linearmotor komplett eingezogen ist. Der Motor fährt komplett aus und währenddessen wird der Strom permanent gemessen, um das Maximum zu suchen. Nach dem Motor voll ausgefahren ist, zieht er sich wieder ein, bis das Maximum erreicht wurde. Abbildung 2.25 zeigt diesen Prozess:

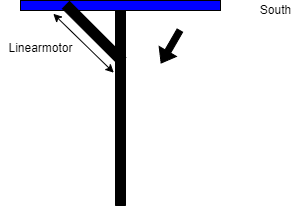
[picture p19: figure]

Abbildung 2.25

Es wurden spezielle Bibliotheken in der Arduino IDE verwendet: Wire.h, INA219_WE.h, Stepper.h

Die Wire.h beinhaltet Funktionen, die für die I²C-Schnittestelle gemacht wurden. Sie erleichtert das Kommunizieren mit der I²C-Komponente wie Register einlesen und speichern oder Daten ganzzahlig schicken und empfangen.

Die INA219_WE.h beinhaltet Funktionen, die für den Stromsensor gemacht wurden. Diese Library benötigt die Wire.h um zu funktionieren. Mit ihre kann der Stromsensor initialisiert werden und die ihre Register ausgelesen werden.

Die Stepper.h beinhaltet Funktionen, mit der Schrittmotoren angesteuert werden können. Genauer gesagt wird mit den H-Brücken kommuniziert, die wiederum die Schrittmotoren ansteuern. Die Geschwindigkeit und wie viele Schritte gemacht werden können mit den Funktionen kontrolliert werden.

Die verwendete Funktionen:

INA219_WE(0x40) → Erstellung des Objektes und Definition der Adresse

ina219.setADCMode(SAMPLE_MODE_128) → stellt den Modus des ADCs ein (12bit, 128 Proben)

ina219.setMeasureMode(CONTINUOUS) → stellt die Messmethode ein (kontinuierlich)

ina219.setPGain(PG_40) → stellt den PGA ein (Gain_40, max. 40mV)

ina219.getCurrent_mA() → gibt den Strom des Sensor in Milliampere zurück

ina219.getOverflow() → überprüft, ob ein Datenregister übergelaufen ist

Stepper motor(stepsPerRevolution, 8, 9, 10, 11) → Erstellung des Objektes, Pins für Ansteuerung werden definiert und Schritte pro Umdrehung angegeben

motor.setSpeed(5) → stellt die Geschwindigkeit auf 5 ein

motor.step(1) → der Schrittmotor geht so viele Schritte wie angegeben (1 Schritt)

Mit den ausgewählten Funktionen kann ein Algorithmus erstellt werden, der das Solarpanel regelt.

# 1.7.1. Regelung des Azimuts

In der Abbildung 2.26 wird ein Programmteil gezeigt, und zwar die Regelung des Azimuts.

Abbildung 2.26: Regelung des Azimuts

Wie zu sehen ist, wurde eine Funktion für die Regelung des Azimuts erstellt. Diese kann mehrmals im Hauptprogramm aufgerufen werden. Wichtig dabei ist, dass ein Parameter mit angegeben werden muss. Nämlich müssen die Schritte angegeben werden, die der Schrittmotor nach links und rechts macht. Daraus ergibt sich der erwünschte Winkel zwischen Süden und Westen bzw. Osten. Am Anfang sind es 90° und späte 15°. Gleich nach der Ausführung der Funktion azimut werden Variablen initialisiert, die nach der Funktion gelöscht werden. Nach der Initialisierung beginnt eine for-Schleife, die von 0 ausstartet und immer weiter inkrementiert wird, bis die angegebene Schrittanzahl erreicht wurde. In der Schleife geht der Schrittmotor einen Schritt gegen den Uhrzeigersinn, weil das Solarpanel wegen den Zahnräder sich invertiert zum Motor dreht. Danach wird der Strom gemessen, gespeichert und ausgegeben. Falls der jetzige Stromwert größer ist als der höchste gemessene Strom, dann wird der Höchstwert mit den jetzigen ersetzt. Dabei wird auch die jetzige Position bzw. wie viele Schritte bereits gemacht wurden gespeichert. Nach der Schleife sollte der höchstmögliche Wert zwischen Süden und Westen und ihre Position gespeichert sein. Danach dreht sich das Solarpanel zurück zur Nullposition bzw. nach Süden. Dieser Vorgang wird mit der anderen Seite von Süden nach Osten wiederholt. Somit gibt es zwei Höchstwerte. Je nachdem welcher größer ist, dreht sich das Solarpanel zum größeren Wert.

# 1.7.2. Regelung der Elevation

Abbildung 2.27 zeigt den zweiten Teil der Regelung der Elevation.

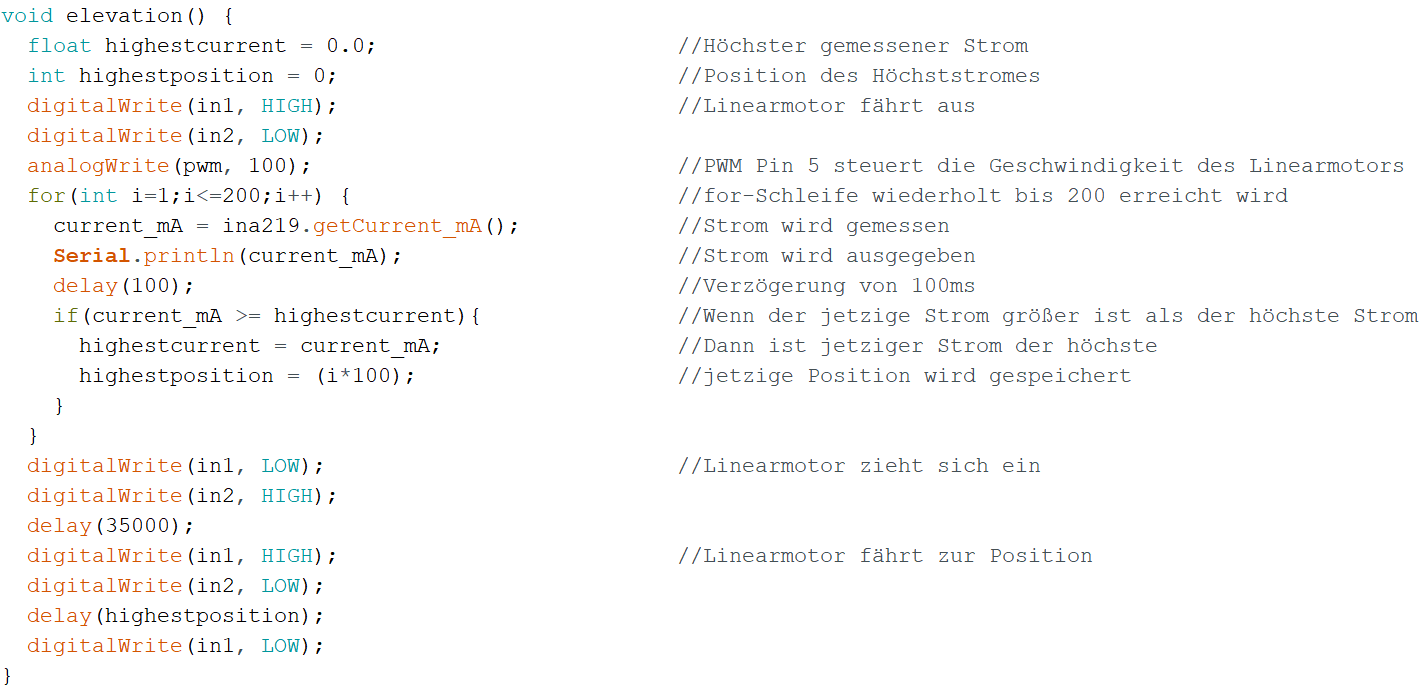
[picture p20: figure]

Abbildung 2.27: Regelung der Elevation

Auch wurde für die Regelung der Elevation eine Funktion erstellt. Das Solarpanel ist senkrecht zu ihrer Stange. Das wird als Nullposition definiert. In diesem Zustand ist der Motor komplett eingezogen. Ist Pin in1 auf HIGH und in2 auf LOW, so fährt mit einer gewissen Geschwindigkeit, die vom Pin pwm ausgeht, aus. Die for-Schleife wiederholt sich 200 Mal, weil das Solarpanel 20 Sekunden braucht, damit es komplett ausgefahren ist. Das heißt, wenn ein Bereich in 100ms aufgeteilt wird, bekommt man 200 Bereiche. Angefangen wird mit einer Strommessung. Ist der jetzige Wert größer als der höchste gemessene Strom, dann wird der Höchstwert mit den jetzigen ersetzt. Dabei wird auch die jetzige Position bzw. wie viele Zeit vergangen ist gespeichert. Dann wird 100ms abgewartet und die Schleife startet von neuem. Nach der Schleife zieht sich der Linearmotor wieder ein. Das dauert 35 Sekunden. Anschließend fährt er wieder aus, aber zur Stelle wo das Maximum war. Dabei wird die Zeit als Einstellparameter genommen.

Ab wann startet und lohnt sich die Regelung?

Es wurde definiert, dass alle Stunden eine Regelung stattfinden soll. Mit der Regelung soll eine maximale Einstrahlung der Sonne auf das Panel erreicht werden. Das heißt, wenn die Sonne von Wolken abgedeckt wird, lohnt es sich nicht. Der Stromsensor kommt bei solchen Wetterzuständen nur auf wenige Milliampere. Um schlechtes Wetter zu umgehen, wird ein Minimumwert definiert.

Mit Hilfe der Aufzeichnung des Sonnenverlaufes des Miniaturpanels in Winter können Minimalwerte für alle Stunden definiert werden. Vom Sonnenaufgang bis Untergang wurde pro Stunde der Strom gemessen. (Abbildung 2.28)

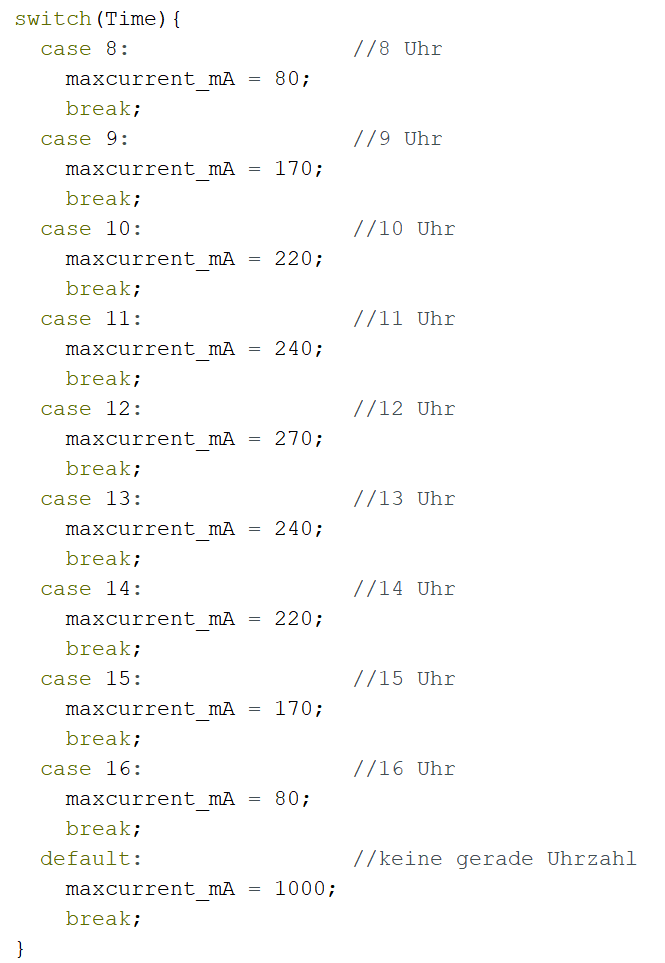
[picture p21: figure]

Abbildung 2.28: Zeitverlauf

Dieser Zeitverlauf ist für den Winter gedacht. Von 8 bis 16 Uhr wird ein Minimalwert pro Stunde zugeordnet. Dazwischen ist der Wert 1000. In dieser Zeit wird die Regelung nie ausgeführt.

Zu Beginn der Regelung muss das Solarpanel in den Nullpunkt gebracht werden. Das Programm macht dies automatisch nach jedem Neustart (Abbildung 2.29).

Abbildung 2.29: Nullpunktposition

Der Schrittmotor dreht in Uhrzeigersinn so lange weiter, bis der Hallsensor einen Magnet in der Nähe erkennt. Danach zieht sich der Linearmotor für 35 Sekunden ein. Damit wird garantiert, dass der Linearmotor voll eingezogen wird.

# 1.7.3. Alternative Regelung

Abbildung 2.30 zeigt eine andere Variante der Regelung:

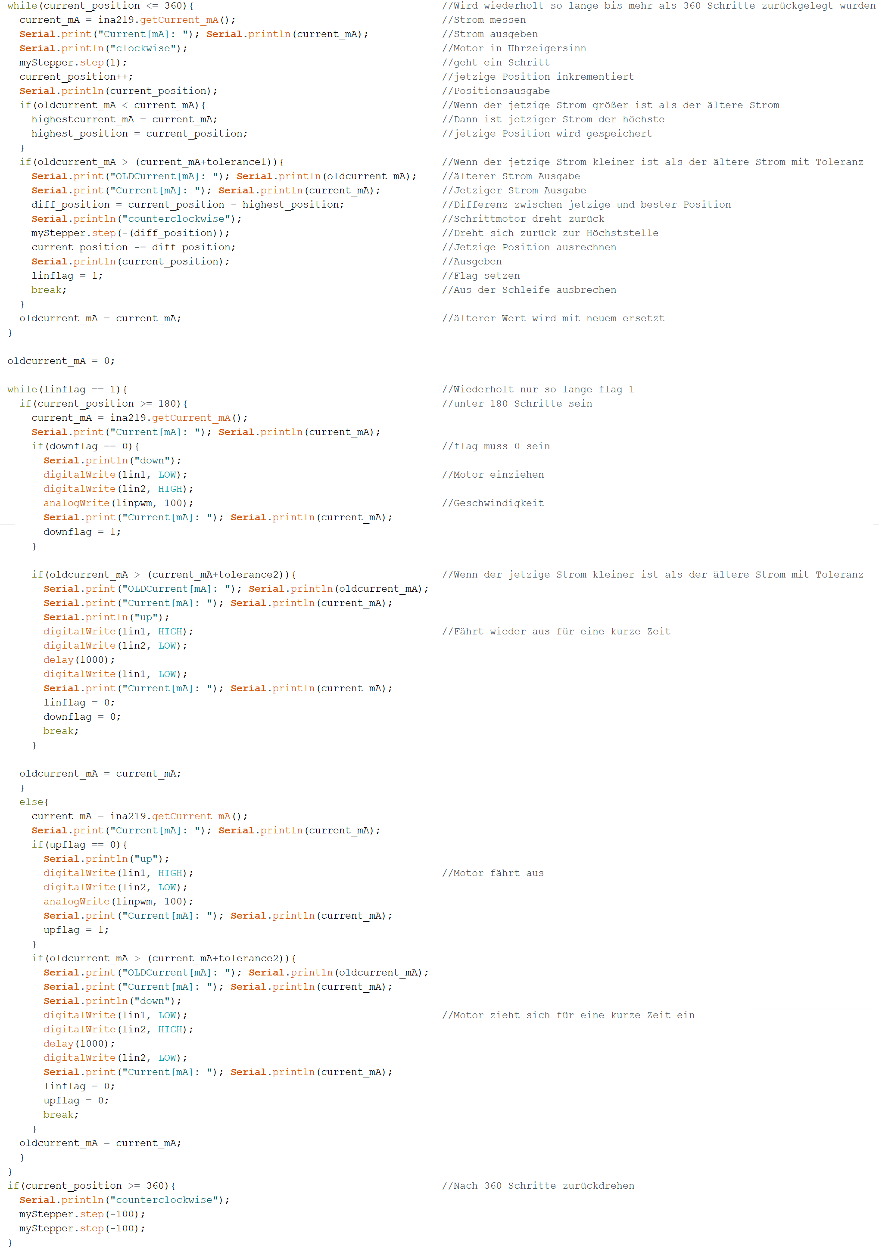
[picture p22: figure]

Abbildung 2.30: Alternativprogramm

Das Alternativprogramm ist energiesparender als das andere. Dieser Algorithmus hört auf, wenn das Solarpanel sich bereits um 180° gedreht hat. Angefangen mit dem Azimut dreht sich der Schrittmotor immer um einen Schritt weiter und der Strom wird dabei mitgemessen. Falls der vorherige Strom kleiner ist als der neu gemessene, wird dieser und seine Position gespeichert. Da die Sonne immer von Osten nach Westen wandert, dreht sich der Motor immer nur in eine Richtung. Außer der vorherige Stromwert ist größer als der aktuelle Wert, dann wird auf die letzte Höchstposition zurückgedreht. Wenn dieser Fall nicht auftritt, wird der ältere Wert mit dem neuem ersetzt und der Vorgang wiederholt sich.

Bei der Regelung der Elevation wird das gleiche Prinzip eingesetzt. Von Osten bis Süden wird der Linearmotor eingezogen, da die Sonne weiter aufgeht. Bei der zweiten Hälfte wird ausgefahren, weil die Sonne dieses Mal untergeht. Nach den beiden Zyklen dreht sich der Schrittmotor zurück Richtung Osten.

Diese Methode ist energieeffizienter, weil sie nicht die Sonne bzw. Lichtquelle sucht, sondern den vorherigen Wert mit dem aktuellen vergleicht. Deshalb wird insgesamt weniger Weg zurückgelegt.

# 1.7.4. Flussdiagramm

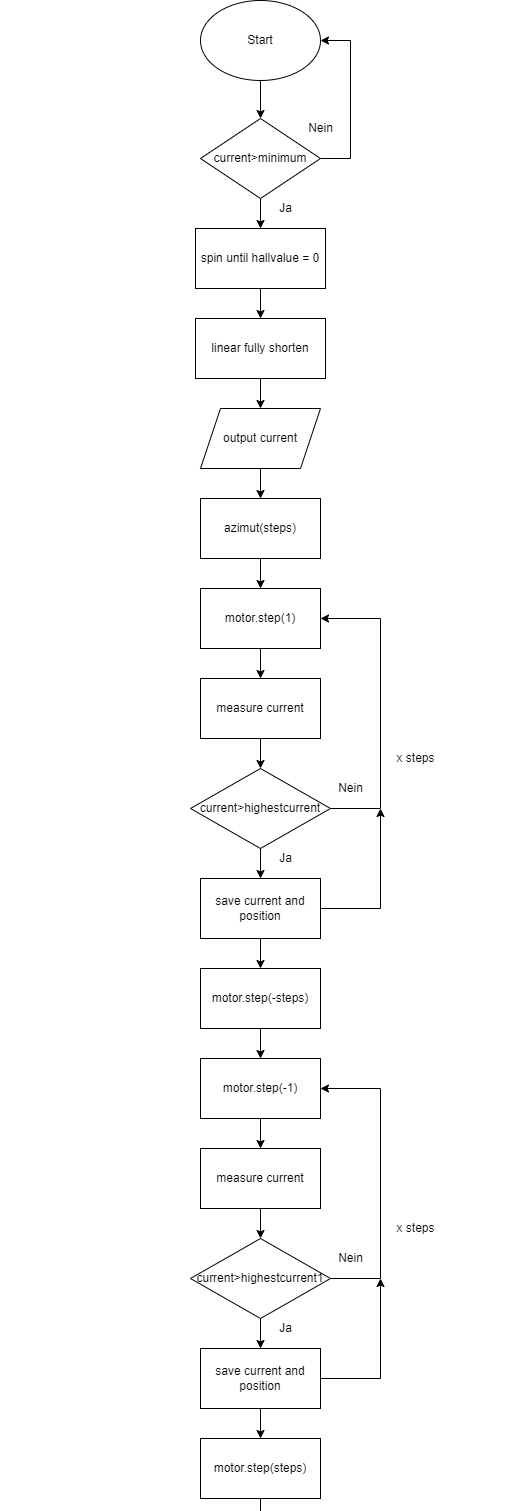
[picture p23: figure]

Abbildung 2.31: Flussdiagramm

# Messungen

Es werden Messungen durchgeführt, um die Theorie in die Praxis zu zeigen.

# 1.8. Kennlinie des Miniaturpanels

Eine Kennlinie einer Solarzelle besteht aus einer Spannung-x-Achse und aus einer Strom-y-Achse (Abbildung 3.1).

Abbildung 3.1: Solarzelle-Kennlinie

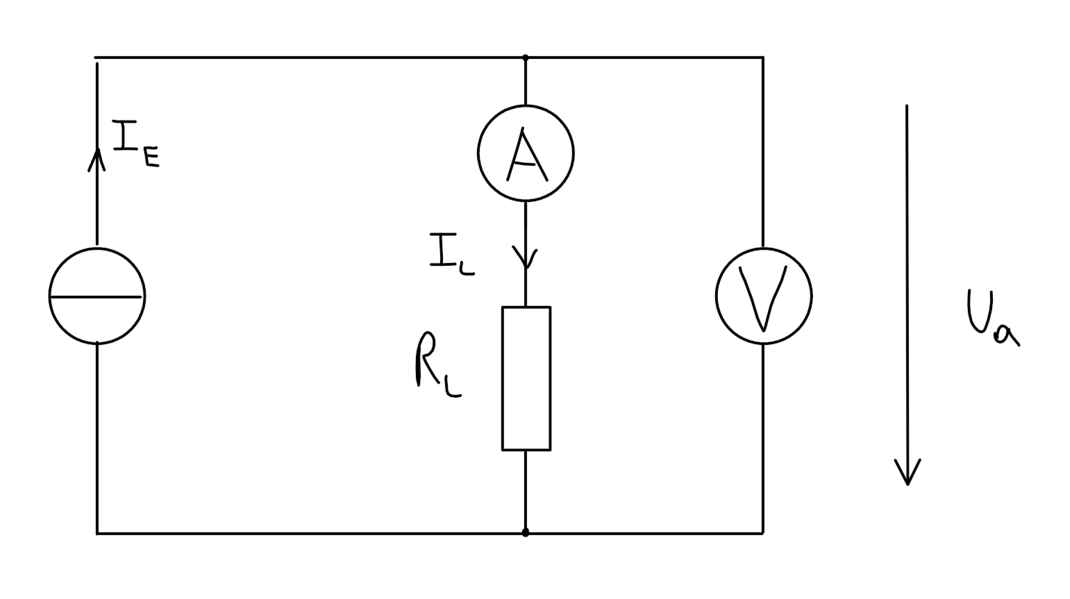
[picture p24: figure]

Abbildung 3.2: Messaufbau

Am Tag der Messung war es bewölkt. Es wurde stromrichtig gemessen, weshalb die Strommessungen genauer waren. Der Lastwiderstand war veränderbar. Die Fläche der Kennlinie beschreibt die Leistung pro Quadratmeter.

# 1.9. Sonnenverlauf des Miniaturpanels

Der Sonnenverlauf an mehreren Tage des Miniaturpanels wurde im Winter aufgezeichnet. Von 8 Uhr bis 16 Uhr wurde pro Stunde einmal gemessen und bei wolkenlosen Wetter mit Sonnenschein (Abbildung 3.3).

Abbildung 3.3: Sonnenverlauf

Am Höhepunkt der Sonne wird am meisten Strom gemessen. Jedoch wird der maximal Strom des Solarpanels nie erreicht, weil in Winter die Sonneneinstrahlung schwächer ist. Das dient als Basis für die Regelung. Dabei wurde das Solarpanel direkt in die Sonne gehalten und vom Stromsensor gemessen.

# 1.10. Sonnenstatistik des Miniaturpanels

Das Solarpanel wurde an einem fixen Punkt in Richtung Süden zeigend über einer Woche gemessen. Die Statistik (Abbildung 3.4) zeigt Punkte an mit unterschiedlichen Farbe, die an unterschiedlichen Tagen und Uhrzeiten gemacht wurden.

Abbildung 3.4: Sonnenstatistik

Die Legende unten erläutert den Tag an den die Messungen gemacht wurden. Wird das über ein Jahr gemacht, kann herausgefunden werden, wann es sich lohnt, die Nachregelung des Solarpanel zu verwenden.

# 1.11. Rentabilitätsrechnung

Theoretische Erzeugung | | Komponente | Verbrauch in W
| | Solarpanel | 90

Theoretischer Verbrauch (während Regelung)
| | DC/DC Wandler
| | Relais | 1,6
| | Schrittmotor | 3,75
| | Linearmotor | 6
| | ESP32 | 0,255
| | H-Brücken | 0,36
| | GPS-Modul | 0,3
| | Stromsensor | 0,0035
| | Summe | 12,2685

Das Solarpanel erzeugt laut Datenblatt 90W, während der Regelung wird 12,3W verbraucht. Das heißt, dass das System in der Theorie mehr erzeugt als es verbraucht.

Erkenntnis

Durch die Messungen kann interpretiert werden, dass es mehr Sinn macht, das Panel bei sonnenintensiven Tagen nach zu regeln. Die Regelung lohnt sich nicht, wenn die meiste Zeit des Tages bewölkt ist. Die Regelung in der Winterzeit in unseren Breitengraden ist ineffizienter, da die Sonneneinstrahlung schwächer ist und wenige sonnenintensive Tage auftreten. Deshalb kann argumentiert werden, dass im Winter das Solarpanel nicht nachgeführt wird, sondern es soll eine möglichst optimale Position einnehmen.

Insgesamt 252 Stunden

# Literaturverzeichnis

Haager, D. D. (2016). Regelungstechnik. Hölder-Pichler-Tempsky GmbH.

# Quellenverzeichnis

[1] abi-physik, Photoeffekt (2022)

[2] lernhelfer, äußerer lichtelektrische Effekt (2022)

[3] photovoltaiksolarstrom, Elektronenlochpaar (2022)

[4] photovoltaiksolarstrom, Raumladungszone (2022)

[5] photovoltaiksolarstrom, Silizium (2022)

[6] regenerative-energie24, Kennzahlen (2022)

[7] fh-bielefeld, Photovoltaik (2022)

[8] solar.forschendes-lernen, Solarkoffer Versuche (2022)

[9] regenerative-zukunft: Schünemann, Christoph, (24.04.2021)

[10] eon, Lebensdauer-Solarzelle (2022)

[11] bootspruefung, azimutelevation (2022)

[12] Regelungstechnik, Haager, DI Dr. Wilhelm, Hölder-Pichler-Tempsky GmbH, 2016

[13] at.rs-online, Hall-Sensor (2022)

[14] rohm, shunt.resistors (2022)

[15] datasheet.ciiva, a1120lua-t-26928941 (2022)

[^1] (Haager, 2016)
[^2] (Haager, 2016)

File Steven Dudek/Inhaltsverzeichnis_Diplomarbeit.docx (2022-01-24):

Struktur Diplomarbeit:

Inhaltsverzeichnis:

Blockschaltbild

Komponentenliste

Zeitplan

Mechanische Arbeit, mechanische Leistung und elektrische Leistung

Solarcontroller

Milestones

Messung mit Leistungswiderstände

H-Brücke oder Vierqudrantensteller

Dual H-Brücke

Entscheidung für L298N

Panel Test

Valenzband – grundlagen halbleiter

Photodiode, Phototransistor, usw. (Auswahl)

Firma Fleck

Layout

Rentabilitätsrechnung

Inbetriebnahme

Spannungsregler/DC-DC Wandler

Messungen

Dimensionierung

Step-Down theorie

Art der Spule

Anwendungsbereiche Kondensatoren

MOSFET

USB-Ports

Shottky-Diode

Maße der Bauteile

AWG - leitungen

Entwicklerboard

Schraubklemmen

Relai/Relaischaltung

Library Loader

Verlustleistung/Wärme

LTSpice/Simulation (Voltage Controll Switch)

Fehlersuche

steuerung-regelung

Motorenauswahl

Mechanik

stromsensor

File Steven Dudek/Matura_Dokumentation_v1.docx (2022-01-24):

1. DC-DC-Wandler (Abwärtswandler)

Der Abwärtswandler (auf Englisch: Buck-Converter, Step-down-Converter) wandelt eine Eingangsspannung in eine niedrigere Ausgangsspannung. Er wird auch Tiefsetzsteller genannt.¹


Abbildung 1: Grundschaltung eines Abwärtswanlder

Der Schalter (bei uns ein NMOSFET) wird mit einer Spannungsgesteuerten Quelle ein- und ausgeschaltet. Üblicherweise werden reichen die Schaltzyklen von einigen Stück bis mehrere Millionen pro Sekunde. Es unterscheiden sich 2 Phasen bei der Schaltung. Im geöffneten Zustand ermöglichen die beiden Energiespeicher Spule und Kondensator die Versorgung an der Last.

¹ Quelle: http://schmidt-walter-schaltnetzteile.de/snt/snt_deu/sntdeu2.pdf

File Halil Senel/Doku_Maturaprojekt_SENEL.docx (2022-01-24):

# Dokumentation Maturaprojekt

Motorauswahl:

Es wird ein Schrittmotorotor benötigt, welches ca. 20kg drehen kann. Das Solarpanel hat ein Gewicht von 8kg und die Alustangen 10kg. Daher wurden Motoren gesucht, welche ein hohes Drehmoment haben. Die Motordrehzahl muss nicht hoch sein, da wir das Panel nur jede halbe Stunde bewegen werden und wir keine schnelle Bewegung brauchen. Durch eigenes Wissen und Berechnungen wurden entschieden ein Drehmoment von ca. 2Nm zu nehmen. Dieser Teil wird noch bearbeitet (Notiz)

## Schrittmotoren

Ein Schrittmotor ist ein Synchronmotor, bei dem der Rotor durch ein gesteuertes, schrittweise rotierendes, elektromagnetisches Feld der Statorspulen um einen kleinen Winekl bzw. Schritt oder sein Vielfaches gedreht werden kann. Schrittmotoren gibt es auch als Linearmotoren.

Positionierung Schrittmotoren:

Ein Schrittmotor besteht aus einem stationären Stator und einem darin rotierenden Rotor. Das Drehmoment, das den Rotor antreibt, entsteht durch die unterschiedlich angeordneten Magnetfelder in Stator und Rotor. Der Rotor dreht sich immer so, dass der größtmögliche magnetische Fluss entsteht. Im Vergleich zu anderen Motoren hat der Stator eines Schrittmotors nur Spulen. Die Drehbewegung wird durch das gezielte Öffnen und Schließen der einzelnen Windungen erzeugt. Dies ist der einfachste Weg, um die Richtung und Geschwindigkeit der Motordrehung zu steuern. Um die Position des Rotors ausgehend von der Startposition zu bestimmen, reicht es aus, die Anzahl der Schritte im oder gegen den Uhrzeigersinn zu zählen und mit dem Schrittwinkel zu multiplizieren.

Schrittmotoren haben viele Vorteile. Hier sind einige aufgelistet:
• Genaue Positionierung
• Haltemoment in Ruhelage
• Günstige Antriebslösung mit hoher Genauigkeit
• Einfacher Aufbau des Treibers

Arten von Schrittmotoren:


Reluktanz-Schrittmotoren:

Bei einem Reluktanz-Schrittmotor besteht der Rotor aus einem Weicheisenkern mit Zähnen. Reluktanzmotoren waren eine Zeit lang sehr beliebt, da sie sehr günstig waren. Doch ein Nachteil von diesen Motoren ist, dass sie ein geringes Drehmoment haben. Da der Weicheisenkern selbst keine magnetischen Pole bildet, hat der Reluktanzmotor kein Rastmoment.

Vorteil: Nachteil:

*) Hohe Geschwindigkeit *) Kleines Drehmoment

*) Genauer Schrittwinkel


Permanentmagnet Schrittmotor:

Bei einem Permanentmagnet-Schrittmotor besteht der Rotor aus zylindrischen Permanentmagneten mit radialer Magnetisierung. Daher kann nur eine begrenzte Anzahl von magnetischen Polen nebeneinander angeordnet werden, was zu einem ziemlich großen Schrittwinkel führt.

Vorteil: Nachteil:

*) günstig *) große Schrittwinkel (ungenau)

*) größeres Drehmoment als beim Reluktanzmotor *) magnetische Verluste

*) größeres Rotor Trägheitsmoment


Hybridschrittmotor:

Hybrid-Schrittmotoren vereinen die Vorteile beider Bauformen. Sein Rotor besteht aus einem axialen Permanentmagneten mit an den Enden angerachten gezahnten Kappen. Die beiden Positionen sind eine halbe Zahnbreite voneinander entfernt sodass sich Nord- und Südpol abwechseln. Hybrid-Schrittmotoren sind heute die am weitesten verbreitete Motor Art und in vielen verschiedenen Ausführungen erhältlich.

Vorteile: Nachteile:

*) Hohes Drehmoment *) Magnetische Verluste

*) Genauer Schrittwinkel

Schrittauflösung:

Die physikalische Schrittauflösung des Motors hängt von der Anzahl der einzeln ansteuerbaren Phasen und der Polpaarzahl ab. Da mit der Erhöhung der Phasenzahl auch der Schaltungs- und Verdrahtungsaufwand zunimmt, wird die Auflösung des Motors im Wesentlichen durch die Polpaarzahl bestimmt. 2-Phasen-Motoren sind am weitesten verbreitet. Es gibt auch 5-Pol-Motoren, besonders geeignet für Mikroschritt und 3-Pol-Modelle, die einen Kompromiss zwischen den beiden Varianten im Betriebsverhalten und Hardware-Aufwand darstellen.

Beispiel:

2 Phasen: 0,9°, 1,8 °

3 Phasen: 1,2 °

5 Phasen: 0,72 °

Ansteuertechnik:


Man unterscheidet zwei Gruppen von Motoren bzw. Ansteuerungstechniken. Unipolare und bipolare Motoren. Beim Bipolarbetrieb werden die Spulen umgepolt und beim Unipolarbetrieb liegt die Versorgungsspannung fest am Mittelabgriff der Spule. Wobei beim Unipolarbetrieb immer abwechselnd ein Spulenende nach Masse gezogen wird. Wegen des hohen Schaltungsaufwandes bei bipolarer Beschaltung war die unipolare Schaltung lange sehr beliebt, obwohl sie wegen der kleineren Spulenströme ein kleineres Drehmoment und kleinere Drehzahlen erzeugt. Mit dem Aufkommen kostengünstiger integrierter Schaltungen begann die bipolare Steuerungstechnologie immer beliebter zu werden.

Unipolar:

Unipolare Motoren haben zwei Wicklungen in der Mitte. Sie haben fünf oder sechs Anschlüsse. Mit einem Multimeter lässt sich schnell feststellen, welcher Anschluss der Mittelabgriff und welcher das Spulenende ist. Es wird gesteuert, indem abwechselnd ein Ende der Spule eingeschaltet wird, so dass jeweils nur die Hälfte der Spule bestromt wird.

Bipolar:

Bipolare Zweiphasenmotoren haben zwei Wicklungen, manchmal zwei Wicklungspaare, die durch Umpolen angesteuert werden. Bei zwei Wicklungspaaren können die Spulenpaare parallel oder in Reihe geschaltet werden, was unterschiedliche Eigenschaften ergibt. Die Parallelschaltung bringt mehr Drehmoment im höheren Drehzahlbereich, stellt aber auch höhere Anforderungen an den Stromregler. Prinzipiell können 8-fach geschaltete Bipolarmotoren auch unipolar betrieben werden, allerdings geht dabei ein Teil des Wirkungsgrades des Motors verloren.

Ansteuerung:

Schrittmotoren drehen bei jeder Wicklungsumkehr einen "Schritt". Erfolgt die Änderung schnell genug, beginnt der Rotor zu rotieren. Durch die Steuerung der Spulen kann der Drehwinkel jederzeit exakt bestimmt werden.


Normalbetrieb:

Beide Spulen werden immer gleichzeitig bestromt. Es ergeben sich vier unterschiedliche Schrittpositionen pro Umlauf.


Wavedrivebetrieb:

Hier wird immer nur eine Spule bestromt. Die Leistungsaufnahme und damit auch das Drehmoment sind im Vergleich zum Normalbetrieb geringer.


Halbschrittbetrieb:

Kombination aus Normalbetrieb und Wavedrivebetrieb. Es werden wechselweise eine bzw. zwei Spulen bestromt. Es gibt 8 Stufenpositionen. Daher auch die Bezeichnung Halbschritt, weil der physikalische Schrittwinkel des Motors halbiert wird. Größere Auflösung, aber kleineres Drehmoment.

5AHEL Halil Senel

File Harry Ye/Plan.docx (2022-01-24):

Plan für die nächsten Wochen Stand 20.01.22

27.01.22

- Motorbefestigung + Gerüst des Solarpanels stabilisieren (Mechanik: Senel)
- Footprint in KiCad beginnen (Hardware: Dudek)
- Überlegung welche Messungen gemacht werden (Alle)

03.02.22

- Regelung + Software GPS testen (Software: Kereku, Ye)
- Footprint fertigstellen (Hardware: Dudek)
- Messungen durchführen (Messung: Ye)
- Mechanische Zeichnung in FreeCad beginnen (Mechanik: Senel)
- Teile der Doku schreiben + Struktur erstellen (Alle)

10.02.22 (Semesterferien)

- Doku schreiben (Alle)
- Zeichnung in FreeCad weitermachen (Mechanik: Senel)
- Footprint fertigstellen (Hardware: Dudek)

17.02.22

- Entwicklerboard fertigstellen (Hardware: Dudek)
- Hardware mit Mechanik zusammenführen (Alle)
- Doku schreiben (Alle)

24.02.22

- Software und Regelung Zusammenführung beginnen (Software: Kereku, Ye)
- Doku schreiben (Alle)

03.03.22

- Software und Regelung zusammenführen (Software: Kereku, Ye)
- Doku schreiben (Alle)

10.03.22

- Fehlerbehebungen bzw. Fehler suchen und optimieren (Alle)
- Doku schreiben (Alle)

17.03.22

- Fehlerbehebungen bzw. Fehler suchen und optimieren (Alle)
- Doku schreiben (Alle)

24.03.22

- Fehlerbehebungen bzw. Fehler suchen und optimieren (Alle)
- Doku optimieren (Alle)

31.03.22

- Fehlerbehebungen bzw. Fehler suchen und optimieren (Alle)
- Abschluss der Dokumentation (Alle)

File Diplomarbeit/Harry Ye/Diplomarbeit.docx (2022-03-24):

# 1. Photovoltaik: Stromerzeugung durch Sonnenenergie

Die Photovoltaik ist ein Prozess, bei der die Lichtenergie mit Hilfe von Solarzellen direkt in elektrische Energie umgewandelt wird. Diese Form der Energieerzeugung zählt zu den erneuerbaren.

# 1.1. Photoelektrischer Effekt

Unter dem photoelektrischem Effekt (Photoeffekt oder lichtelektrischen Effekt) versteht man die Wechselwirkung der Elektronen mit dem Photonen des Lichtes. Dabei nehmen die Elektronen die Photonen auf besser gesagt ihre Energie und lösen sich aus der Bindung des jeweiligen Stoffes. Diese Energie kann mit der Formel

| E=h∙f | (1.1)

E…Energie

h…Planck’sches Wirkungsquantum

f…Frequenz

berechnen. Um sich herauslösen zu können, muss die Photonenenergie größer als die Bindungsenergie des Elektrons sein. Es gibt drei Arten des photoelektrischen Effekts: äußeren, inneren und Photoionisation, wobei auf den inneren photoelektrischen Effekt genauer eingegangen wird.

# 1.1.1. Äußerer photoelektrischer Effekt

Dieser Effekt wird auch als Photoemission oder Hallwachs-Effekt bezeichnet. Er beschreibt das Herauslösen der Elektronen aus einem Halbleiter- oder Metalloberfläche, wenn sie mit Licht bestrahlt wird. Dazu muss die Photonenenergie größer als die Austrittsarbeit des Materials sein. Abbildung 1.1 veranschaulicht dieses Phänomen.


Abbildung 1.1: Äußerer photoelektrischer Effekt

Mit der Gegenfeldmethode kann der Effekt demonstriert werden und die Austrittsarbeit bestimmen werden.

# 1.1.2. Innerer photoelektrischer Effekt

Dieser Effekt tritt ausschließlich in Halbleiter auf. Zwei Fälle beschreiben diesen Effekt: Photoleitung und photovoltaischer Effekt.

# 1.1.2.1. Photoleitung

Wenn durch die Lichtbestrahlung die Leitfähigkeit eine Halbmaterials erhöht wird, spricht man von der Photoleitung. Um diesen Effekt besser verstehen zu können, ist das Bändermodell (Abbildung 1.2) abgebildet.


Abbildung 1.2: Bändermodell

Eine externe Photonenenergie wird in den Elektron eingeführt. Daraufhin wird der Elektron auf den höheren Leitungsband gehoben. Die Photonen müssen so viel Energie aufbringen, bis die Elektronen die Bandlücke bzw. verbotenen Zone überwunden haben. Während dieses Prozesses hinterlässt das Elektron ein Loch im Valenzband. So kommt es zur Bildung eines Elektronen-Loch Paars. Das Elektron im Leitungsband ist nun frei beweglich.

# 1.1.2.2. Photovoltaischer Effekt

Durch das Prinzip der Photoleitung kann mit einem Halbleiter Licht in elektrische Energie umgewandelt werden. Dazu wird die Funktion einer Diode und seiner Raumladungszone gebraucht. Die Photonen brechen die Elektronenpaarbindungen auf. Wenn ein Verbraucher angeschlossen wird, ziehen sich die freibeweglichen Teilchen an und ein Strom beginnt zu fließen. Abbildung 1.3 stellt den Aufbau und die Funktion einer Solarzelle dar.


Abbildung 1.3: Solarzelle

# 1.2. Silizium-Solarzelle

Eine Solarzelle wandelt auf Grund des photovoltaischen Effektes Sonnenlicht in elektrische Energie um. Sie besteht aus einem Halbleitermaterial, wie Galliumarsenid, Cadmiumtellurid oder Chalkopyrite. Jedoch ist Silizium das häufigste verwendete Halbleitermaterial, weil es in großen Mengen zur Verfügung steht. Silizium-Solarzellen unterscheiden sich in zwei Arten: dickschichtig und dünnschichtig. Zu den Dickschichtzellen zählen die monokristalline und polykristalline Zellen und die amorphe Zelle gehört zu den Dünnschichtzellen.

# 1.2.1. Herstellung

Als Erstes wird aus Quarzsand Silizium gewonnen. Das Silizium wird zu Ingots verarbeitet. Danach werden die Ingots durch das Sägen zu Wafer. Die Wafer werden zu Solarzellen verbaut. (Abbildung 1.4)


Abbildung 1.4: Herstellung

# 1.2.2. Verschiedene Arten

Monokristallin: Solche Solarzellen bestehen aus einkristallinem Silizium, weshalb der Siliziumanteil sehr hoch ist. Der Wirkungsgrad einer monokristalline Zelle liegt bei ca. 20%. Sie ist vergleichsweise teurer als die anderen wegen der aufwendigeren Produktion.

Polykristallin: Bei den polykristalline Zellen ist das Silizium nicht so rein. Dadurch ist die Produktion weniger aufwendig und der Preis ist billiger, weshalb polykristalline Zellen das beste Preis-Leistung-Verhältnis haben. Der Wirkungsgrad liegt bei 15%.

Amorph: Dünnschichtzellen sind nichtkristallin. Das heißt, dass das Silizium mit anderen Materialien vermischt wird und auf eine dünne Schicht aufgetragen wird. Deshalb ist der Wirkungsgrad nur zwischen 5-7%. Jedoch sind sie flexibel und lassen sich falten und rollen. Die Zellen sind günstiger als Dickschichtzellen.

# 1.2.3. Technische Merkmale

# 1.2.3.1. Kenngrößen

In den üblichen Technischen Datenblätter stehen folgende Kennwerte:

- ISC: Kurzschlussstrom
- VOC: Leerlaufspannung
- VMPP: Spannung bei maximaler Leistung
- IMPP: Strom bei maximaler Leistung
- PMPP: Maximale erzielbare Leistung unter STC
- FF: Füllfaktor

Der Füllfaktor ist ein Verhältnis zwischen der Leistung PMPP (Blau) und dem Produkt von ISC und VOC (Gelb) und dementsprechend dimensionslos. Sie gibt die Qualität der Zelle an. Für einen höheren Wirkungsgrad muss der Füllfaktor auch höher sein.


Abbildung 1.5: Füllfaktor

Den Füllfaktor berechnet man sich mit dieser Formel:

| FF=(P_(MPP))/(U_(OC) ∙I_(SC)) | (1.2)

PMPP … maximale Leistung

UOC … Leerlaufspannung

ISC … Kurzschlussstrom

TK PMPP: Koeffizient für die Leistungsänderung abhängig von der Zellentemperatur.

η: Zellwirkungsgrad

| η=(P_(MPP))/(A∙E_e) | (1.3)

A … bestrahlte Fläche

Ee … Bestrahlungsstärke

Aus den Kennwerten kann eine Strom-Spannungs-Kennlinie erstellt werden (Abbildung 1.6).


Abbildung 1.6: Strom-Spannungs-Kennlinie

# 1.2.3.2. Schaltbilder

Das Schaltsymbol einer Solarzelle ist gleich die von einer Leuchtdiode (Abbildung 1.7).

Abbildung 1.7: Schaltsymbol

Ein Ersatzschaltbild schaut folgendermaßen aus (Abbildung 1.8):


Abbildung 1.8: Ersatzschaltbild

Links ist das Schaltzeichen einer Solarzelle und Rechts abgebildet ihr Ersatzschaltbild. Die Gesamtstromstärke wird errechnet mit:

| I=I_(ph) -I_D | (1.4)

# 1.2.4. Solarpanel

Einzelne Solarzellen werden in Reihe bzw. in Serie geschalten (Abbildung 1.9). Dadurch entsteht ein Solarpanel oder Solarmodul. Die Spannungen der jeweiligen Solarzelle werden zusammenaddiert. Werden die Solarzellen parallel geschalten, so werden die Ströme addiert (1.10).


Abbildung 1.9: Reihenschaltung


Abbildung 1.10: Parallelschaltung

Häufig befinden sich Bypass-Dioden bzw. Freilaufdioden in den Solarmodulen. Abbildung 1.11 zeigt eine abgeschattete Solarzelle in einer Reihenschaltung.


Abbildung 1.11: abgeschattete Solarzelle

Diese abgeschattete Zelle wirkt wie ein Widerstand bzw. Verbraucher. Der durchfließende Strom wandelt sich in Wärme um und die Solarzelle überhitzt sich. Das wird Hotspot genannt (Abbildung 1.12).


Abbildung 1.12: Hotspot

Wird nun eine Freilaufdiode antiparallel geschaltet, entsteht ein Kurzschluss und die Diode leitet den Strom um (Abbildung 1.13).


Abbildung 1.13: Bypass-Diode

In der Praxis wird nur eine Bypass-Diode pro Solarmodul verbaut. Das heißt ist ein Solarmodul beschattet, so leitet die Diode den Strom um (Abbildung 1.14).

Abbildung 1.14: eine Bypass-Diode pro Solarmodul

In unserem Projekt wird ein monokristallines Solarpanel verwendet. Technische Daten:

- Nennleistung Pmax: 90W mit einer Toleranz von 5%
- Strom bei Pmax Imp: 5,25A
- Spannung bei Pmax Vmp: 17,98V
- Kurschlussstrom ISC: 5,65A
- Leerlaufspannung VOC: 22,77V
- Gewicht: 7,8kg
- Abmessungen: 1185x545x35mm

# 1.2.5. Wirkungsgrad

Der Wirkungsgrad ist das Verhältnis der Ausgangsgröße und die Eingangsgröße. Beim Leistungsverhältnis einer Solarzelle ist es die erzeugte elektrische Leistung durch die einfallende Strahlung:

| η=(P_(elektrisch))/(P_(Licht)) | (1.5)

η … Wirkungsgrad

Pelektrisch … erzeugte elektrische Leistung

PLicht … einfallende Strahlungsleistung

Wirkungsgrade der verschiedenen Zellarten:

Material | Max. Wirkungsgrad im Labor | Max. Wirkungsgrad Serienproduktion | Typ. Wirkungsgrad Serienproduktion | Flächenbedarf pro kW
Monokristallin | 26,1% | 24% | 19% | 5,3m²
Polykristallin | 22,3% | 20% | 17% | 5,9m²
Amorph | 14% | 8% | 6% | 16,7m²

Der Wirkungsgrad der Solarzellen wird mit den Standard-Test-Conditions gemessen (1000 Watt Lichteinstrahlung, 25 Grad Zelltemperatur, Air Mass von 1,5).

Um den Wirkungsgrad einer Solarzelle technisch zu verbessern, muss das Material mehr Lichtwellen des Spektrums verarbeiten können. Tandem-Solarzellen bestehen aus verschiedenen Stapeln von Materialien, somit wird ein breiteres Spektrum abgedeckt.

Eine Solarzelle kann auch Wirkungsgrad verlieren. Wenn die Zelltemperatur zu hoch ist, verliert die Zelle an Wirkungsgrad, weil sie weniger Leistung erzeugt. In der Regel nach den STCs sinkt die Leistung um 0,4% pro Grad Celsius. Außerdem haben Solarzellen eine bestimmte Lebensdauer. Bei kristallinen Zellen liegen sie über 30 Jahren und bei amorphen 20 bis 25 Jahren. Von Jahr zu Jahr verringert sich der Wirkungsgrad einer Solarzelle.

# 2. Regelungsentwickelung

# 2.1. Recherche und Vorwissen

Regeln ist das selbsttätige Beeinflussen eines technischen Prozesses (einer Anlage, eines Systems) in gezielter Weise. Dabei handelt es sich um einen geschlossenen Wirkungsablauf; das heißt, die den Prozess beeinflussenden Größen werden mit geeigneten Regeleinrichtungen aus gemessenen Prozessgrößen selbst gebildet und nicht nur von außen vorgegeben.[^1] Abbildung 2.1 veranschaulicht die Regelung einer antiken Wasseruhr.

Abbildung 2.1: Antike Wasseruhr

Bei einer bestimmten Füllhöhe h des Wassers sind der Zufluss und Abfluss gleichgroß ( q_z =q_a ), weil der Schwimmer den Zufluss bei steigender Wasserhöhe verringert.

# 2.1.1. Darstellung eines Regelungssystems

Ein Geräteplan stellt schematisch die gerätemäßige Realisierung einer Regelung dar (Abbildung 2.2).

Abbildung 2.2: Geräteplan

Die Drehzahl des Motors wird gemessen. Anhand des Istwertes wird eine entsprechende Steuerspannung in den Stromrichter geschickt, um den Sollwert anzunähern.

Ein Blockschaltbild stellt die Regelung in Funktionsblöcken dar. Dabei werden die einzelnen Funktionen der Geräte vereinfacht. Abbildung 2.3 zeigt die obige Drehzahlregelung als vereinfachtes Blockschaltbild an.

Abbildung 2.3: Blockschaltbild

# 2.1.2. Regelkreis

Die Abbildung 2.3 zeigt den Aufbau eines Regelkreises. Allgemein schaut der Regelkreis so aus:

Abbildung 2.4: Regelkreis

Elemente:

- Regler: Der Regler versucht die Regelabweichung (Differenz zwischen Sollwert und Istwert) zu eliminieren bzw. auf null zu setzen. Dafür erzeugt er ein entsprechendes Signal.
- Stellglied: Dieses Signal nimmt das Stellglied (z.B. Verstärker, Stromrichter, Servomotor, Ventil) auf. Da das Signal des Reglers eine leistungsschwache Größe ist und die Regelstrecke meist eine leistungsstarke Größe benötigt, dafür wird ein Stellglied eingesetzt, das so eine Stellgröße ausgeben kann.
- Regelstrecke: Die Regelstrecke ist das System, das geregelt wird. Sie gibt die Regelgröße bzw. den Istwert aus.
- Messglied: Das Messglied misst den jetzigen Istwert. Dieser Istwert wird in eine für den Regler verwendbare Größe umgeformt.
- Störgröße: Da Störungen unvermeidlich sind, müssen sie so weit minimalisiert werden, bis sie irrelevant sind. Sie treten während der Regelung der Strecke auf.

Sehr oft wird der Regler und das Stellglied als einen Block zusammengefasst. Das gilt auch für die Regelstrecke und das Messglied. Daraus ergibt sich der Standardregelkreis (Abbildung 2.5):


Abbildung 2.5: Standardregelkreis

Die wichtigsten Größen sind:

- X(s) … Regelgröße (Istwert)
- W(s) … Führungsgröße (Sollwert)
- E(s) … Regelabweichung
- U(s) … Stellgröße
- Z(s) … Störgröße
- FR(s) … Übertragungsfunktion des Reglers
- FS(s) … Übertragungsfunktion der Regelstrecke

Ohne der Rückführung im Regelkreis erhält man den offenen Regelkreis, mit der Übertragungsfunktion FO:

| F_O (s)=F_R (s)∙F_S (s) | (2.1)

Schließt man den Regelkreises, bekommt man die Führungsübertragungsfunktion FW:

| F_W =(F_R ∙F_S)/(1+F_R ∙F_S)=(F_O)/(1+F_O) | (2.2)

# 2.1.3. Regler

Der Regler hat die Aufgabe, die Führungsgröße (Sollwert) mit der Regelgröße (Istwert) zu vergleichen und aus der Differenz beider Größen (Regelabweichung) eine entsprechende Stellgröße zu erzeugen.[^2] Zwischen den elektrischen Reglern unterscheidet man analoge und digitale.

Es gibt drei Grundtypen der analogen Regler:

- P-Regler: Erzeugt eine der Regelabweichung proportionale Stellgröße. Vorteil: Schnelles Reagieren auf Regelabweichung, Nachteil: Regelt nie komplett aus (Ausnahme: Regelstrecke mit I-Anteil)
- I-Regler: Erzeugt eine Stellgröße, die dem zeitlichen Integral der Regelabweichung proportional ist. Vorteil: Genaue Regelung der Abweichung, Nachteil: Langsames Reagieren auf Regelabweichungen
- D-Regler: Erzeugt eine Stellgröße, die der momentane Änderungsrate der Regelabweichung proportional ist. Vorteil: Verbessert das Stabilitätsverhalten des Regelkreises, Nachteil: Regelt nicht aus → nur mit anderen Reglern sinnvoll

Durch Parallelschalten der einzelnen Grundregler erhält man:

- PI-Regler
- PD-Regler
- PID-Regler

Die Aspekte der einzelnen Regler werden kombiniert. Abbildung 2.6 veranschaulicht die Funktionen der Regler (Stellgrößen bei gegebener Regelabweichung):


Abbildung 2.6: Erzeugte Stellgröße

Verglichen zu analoge Regler, die aus elektronische Bauteile (z.B. OPV) bestehen, werden für digitale Regler Computer (z.B. Mikrocontroller) verwendet. Die Regelgröße wird in periodischen Zeitabständen von einem Analog-Digital-Converter kurz ADC in eine digitale Größe konvertiert und vom Rechner eingelesen. Die Führungsgröße wird im Programm eingegeben oder von außen durch einen ADC hineingeschickt.

Abbildung 2.7: Digitaler Regler

Im gespeicherten Programm des Computers arbeitet ein Regelalgorithmus Schritte ab, um die Stellgröße mit der berechneten Regelabweichung zu erhalten. Die Stellgröße kann entweder wieder in ein analoges Signal umgewandelt werden oder durch ein PWM-Signal gesendet werden.

Ein Digital-Analog-Converter wandelt digitale Signal in analoge um. Abbildung 2.8 veranschaulicht die analoge Umwandelung der Stellgröße.


Abbildung 2.8: Analoge Umwandelung

Pro Zeitabstand wird die Stellgröße einmal abgetastet und bis zur nächsten Abtastung wird der Wert konstant gehalten.

Das pulsbreitenmodulierte Signal PWM stellt die Stellgröße als Rechtecksignal mit einer bestimmten Frequenz dar. Das Verhältnis zwischen der Impulsdauer und der Periodendauer, auch Duty-Cycle genannt, ermöglicht das Erzeugen eines bestimmten Stellgrößenwertes (Abbildung 2.9).


Abbildung 2.9: PWM

Da die Erzeugung des PWM-Signals rein softwaretechnisch verläuft, ist ein DAC nicht essenziell.

# 2.1.4. Theoretischer Ansatz

Um das Solarpanel nachregeln zu können, werden zwei Motoren für das Einstellen des Höhenwinkels und des Azimuts benötigt. Zum Regeln der Aktuatoren wird ein Mikrokontroller gebraucht, der Einlesen und Ausgeben kann. Das Messglied soll den Strom eines Solarpanels einlesen können.

Der Mikrokontroller sucht die beste Position mit dem höchsten Lichteinfall, in dem er den Höchstwert des Stromes herausfindet und das Solarpanel wird zu dieser Position nachgeregelt. Abbildung 2.10 zeigt den entworfenen Regelkreis.


Abbildung 2.10: Theoretischer Ansatz

# 2.1.5. Praktischer Ansatz

Für den digitalen Regler wird ein ESP32 verwendet, der alle benötigten Funktionen (Eingebauter ADC, I²C-Schnittstelle, das Erzeugen von PWM-Signalen, usw.) abdeckt (Regler). Das Bewegen des Azimuts beim Solarpanel erledigt ein Schrittmotor und beim Höhenwinkel ein Linearmotor (Stellglied). Im Gegensatz zum großem Solarpanel wird ein kleineres zur Messung des Stroms genommen (Regelstrecke). Das Messen übernimmt ein Stromsensor, der den Stromwert in digitale Spannungsimpulsen umwandelt und über die I²C-Schnittstelle zum Mikrokontroller schickt (Messglied). Im Folgenden werden die für die Regelung verwendeten Komponenten beschrieben.

# 2.2. Stromsensor

Der Stromsensor soll den Strom des kleineren Solarpanels messen und in eine digitale Größe umgewandelt werden, damit der Mikrokontroller den Wert verarbeiten kann. Dabei werden zwischen zwei effektive Arten unterschieden.

# 2.2.1. ACS712: Hall-Sensor

Die erste Variante der Strommessung ist mit einem Hallsensor. Er misst den Strom auf Basis des Halleffekts und wandelt ihn Spannung um. (Abbildung 2.11)

Abbildung 2.11: ACS712

# 2.2.1.1. Halleffekt

Wird ein stromdurchflossener Leiter in der Nähe eines Dauermagnets platziert. Die Ladungsträger bewegen sich senkrecht zum Magnetfeld des Dauermagnets, wodurch sich die geradlinigen Bahnen des Leiters krümmen. Es wirkt eine Lorentzkraft auf den Ladungsträger. Nun sind mehr Ladungsträger auf einer Seite im Leiter. Dadurch entsteht ein Potenzialunterschied, die Hallspannung. Diese Spannung ist abhängig von der Distanz des Magneten zum Leiter. Bei einem digitalen Hallsensor muss der Magnet in einer gewissen Reichweite sein, damit sich das Ausgangssignal ändert. (Abbildung 2.12)

Messung der magnetischen Feldstärke - der Hall-Effekt

Abbildung 2.12: Halleffekt

Die ACS712 Module liefern max. 185 Millivolt pro Ampere. Aus diesem Grund ist der ACS712 ungeeignet für die Regelung, weil dieser Wert zu niedrig ist, für das Miniaturpanel. Die maximale Anzahl der Schritte des ADCs bei einem Maximalstrom von 340mA kann mit Rechnungen ermittelt werden:

| V_(maxACS712) =Sensitivität des ACS712∙A_(maxPanel) =(185mV)/A∙0,34A=62,9mV | (2.3)

VmaxACS712 … Max. Ausgansspannung des ACS712

AmaxPanel … Max. Strom des kleinen Panels

| ADC_(V pro Schritt) =(Referenzspannung des ADCs)/(Auflösung des ADCs)=(3,3V)/(2^12 counts)=0,806mV/count | (2.4)

Aus der ersten Rechnung erhält man die maximale Ausgangspannung des Moduls und aus der zweiten die Spannung pro Schritt des AD-Wandlers des ESP32. Werden die beiden Werte dividiert,

| max. Schritte=(V_(maxACS712))/(ADC_(V pro Schritt))=(62,9mV)/(0,806mV/count)=78,75 counts | (2.5)

erhält man 78 Schritte, die der ESP32 darstellen kann. Das heißt, dass der Unterschied zwischen einen Milliampere nicht festgestellt werden kann. Der Sensor ist für größere Ströme geeignet.

# 2.2.2. INA219: Shuntwiderstand

Durch das Ohm’sche Gesetz kann mit einem Shuntwiderstand Strom gemessen werden.

# 2.2.2.1. Shuntwiderstand

Früher wurde der Shuntwiderstand zur Messbereichserweiterung eines Amperemeters eingesetzt. Dabei wird der Widerstand parallel zum Amperemeter geschaltet (Abbildung 2.13).

Shunt Widerstand [Stromteiler]

Abbildung 2.13: Shuntwiderstand

Durch den Amperemeter mit einem Innenwiderstand r fließt ein Strom Ir. Der Gesamtstrom Im fließt durch den Amperemeter und dem Shuntwiderstand R. Daraus ergibt sich eine Formel:

| I_m =I_r ∙(1+r/R) | (2.6)

Somit kann der Strom Im, der den Messbereich übersteigt, gemessen werden.

Heutzutage wird ein Shuntwiderstand zur Messung von Strömen verwendet. In dem der Spannungsabfall am Widerstand gemessen wird und der Strom mit dem ohmschen Gesetz berechnet wird.

Der INA219 ist ein Bauteil, der die Spannung am Shuntwiderstand misst. Die schematische Darstellung Abbildung 2.14 zeigt den Aufbau des INA219s.


Abbildung 2.14: Schematic INA219

Die Shunt-Spannung, die am VIN+ und VIN- angelegt wird, wird vom PGA Programmable Gain Amplifier verstärkt. Dabei ist es egal, ob die Potenziale vertauscht angelegt werden, denn der INA219 setzt nur ein negatives Vorzeichen vor dem ausgegebenen Wert. Das Besondere am INA219 ist, dass sie die Busspannung messen kann. Das heißt, wenn ein Verbraucher in Reihe geschaltet wird, kann seine Spannung ermittelt werden. Jedoch muss der Verbraucher nach dem Shuntwiderstand geschaltet werden. Diese Verschaltung wird High-Side genannt. Außerdem müssen Versorgung und Verbraucher auf einen gemeinsamen GND verbunden sein. Die Versorgung soll im Bereich von 0 bis 26V sein und bei 0,1Ω sollte der Strom maximal 3,2A sein. Der INA219 selbst muss mindestens mit 3V und höchstens 5,5V versorgt werden.

Wie ihr den INA219 in den zu messenden Stromkreis integriert

Abbildung 2.15: INA219 Spannungen

Wie im Name schon steht, kann der PGA programmiert werden. Dabei gibt es vier mögliche Bereiche, die eingestellt werden können. Die Zahl steht für die maximale Shunt-Spannung in mV, die bei diesem Bereich anliegen darf:

- PG_320
- PG_160
- PG_80
- PG_40

Je niedriger der Bereich, desto genauer bzw. höher ist die Auflösung.

Nach der Verstärkung wandelt der ADC die analogen Signale in digitale um und speichert sie ins jeweilige Register hinein. Auch die Auflösung des ADCs kann geändert werden. Es kann zwischen 9 bis 12 Bit ausgewählt werden. Hier gilt je größer die Auflösung desto länger dauert die Umwandlungszeit. Zum Vergleich: Bei einem 9 Bit dauert es 84µs und bei 12 Bit 532µs. Auch können mehr Proben (Samples) pro Messung eingestellt werden. Der Durchschnitt der Samples ist der tatsächliche Wert. Vorteil ist, dass starke Messabweichung geringe Auswirkung auf den Endwert hat. Nachteil ist die längere Conversion-Time. Bei 12 Bit Auflösung mit 2 Samples dauert es 1,06ms, somit das doppelte zur vorherigen Zeit. Die Zeit und Samples sind direkt proportional zueinander und verdoppeln sich pro Schritt. Das heißt, dass bei 128 Samples die Totzeit bei 68,1ms liegt.

Die umgewandelte Werte vom ADC werden in den jeweiligen Register gespeichert. Der Power Register speichert die Leistung aus der Multiplikation vom Current- und Voltage-Register. Auf Anforderung vom Mikrokontroller werden die gespeicherten Werte abgerufen und per I²C-Schnittstelle transportiert.

Im Datenblatt ist der Schritt pro V vom 12 Bit ADC mit einem PG_40 angegeben. LSB-Schrittgröße ist 10 µV. Die Schrittanzahl der maximalen Shunt-Spannung ist:

| max. U_(Shunt) =max. I_(Shunt) ∙R_(Shunt) =0,34A∙0,1Ω=34mV | (2.7)

max. UShunt … maximale Shunt-Spannung

max. IShunt … maximaler Shunt-Strom

RShunt … Shuntwiderstand

| max. Schritte=(max. U_(Shunt))/(ADC_(V pro Schritt))=(34mV)/(10µV/count)=3400 counts | (2.8)

Verglichen zum ACS712 sind die Counts wesentlich höher und Änderungen der Werte in Mikrobereich werden erkannt.

Es können insgesamt vier Stromsensoren gleichzeitig im Betrieb genommen werden. Die Pins A0 und A1 am INA219 sind für die Änderung der Adresse zuständig. Sie können entweder auf HIGH oder LOW gelötet werden.

Der INA219 hat verschiedene Modi mit jeweiligen Funktionen.

- Kontinuierlich Modus: Misst den Wert andauernd. Auch ohne Anfragen vom µController werden die Register ständig mit neuen Werten aktualisiert.
- Triggered Modus: Es wird nur gemessen, wenn auch eine Anforderung verschickt wurde. Dabei werden alle Messungen auf einmal ausgegeben und gehören zu einem Messzyklus.
- Power-Down Modus: Im Normalbetrieb verbraucht der Sensor 0,7mA. Im Power-Down Modus nur 10µA. Mit einer Funktion kann der INA219 in den Stand-By gebracht werden.

Die Pin-Konfiguration des SOT-23 Gehäuses ist in der Abbildung 2.16 dargestellt.

Abbildung 2.16: Pin-Konfiguration

Name | Pin | In/Out | Beschreibung
IN+ | 1 | Analog Input | Höheres Potential des Shunt-Widerstands
IN- | 2 | Analog Input | Niedriges Potential des Shunt-Widerstands
GND | 3 | Analog | Ground
VS | 4 | Analog | Versorgungsspannung (3 bis 5,5V)
SCL | 5 | Digital Input | Clock-Leitung der I²C-Schnittstelle
SDA | 6 | Digital I/O | Daten-Leitung der I²C-Schnittstelle
A0 | 7 | Digital Input | Adress-Pin der I²C-Schnittstelle
A1 | 8 | Digital Input | Adress-Pin der I²C-Schnittstelle

# 2.2.3. HW-831 Modul

Um den INA219 nutzen zu können, muss dafür ein Modul erstellt werden. Dafür wurde in KiCad ein Schaltungsplan und PCB entworfen (Abbildung 2.17 und Abbildung 2.18). Nur noch die Bauteile haben gefehlt. Leider war der INA219 auf RS-Components nicht verfügbar. Aus diesem Grund wurde ein fertiges HW-831 Modul von Amazon gekauft.


Abbildung 2.17: INA219 Schaltplan


Abbildung 2.18: PCB Design

Die beiden Widerstände an den SCL und SDA Pins sind Pull-Up-Widerstände. Sie ziehen die Leitungen auf die Versorgungsspannung und sind somit auf HIGH-Level, da der Pin eine Open-Collector-Schnittstelle hat. Das heißt, dass der Pin ohne Pull-Up-Widerstände keinen exakten logischen Wert einnimmt, wenn es nicht gerade auf GND gezogen wird. Das kann zu Datenverlust führen. Der typische Wert eines Pull-Up-Widerstands liegt bei 10kΩ. Je niedriger der Widerstand, desto höher ist die Geschwindigkeit der Leitung. Bei höheren Werten ist der Leistungsverbrauch niedriger. Die Adress-Pins sind normalerweise auf GND, aber sie können auf VCC gelötet werden. Das ändert die logische 0 auf eine logische 1 im Register. Der Stützkondensator am VS-Pin stabilisiert die Versorgungspannung. Er wird parallel zur Versorgung geschalten. Die Zuleitung für Speisespannungen und GND zu den ICs sind parasitär induktiv. Das heißt, dass sehr schnelle Stromsteigerungen passieren können, die zu einer sehr schnelle Änderung der Speisespannung führt. Der Kondensator mindert den Stromimpuls, damit die Versorgung nicht einbricht.

Das Layout des HW-831 Moduls ist ein wenig anders, aber die Funktion ist dieselbe (Abbildung 2.19 und Abbildung 2.20).

Abbildung 2.19: Front View des Moduls

Abbildung 2.20: Back View des Modul

# 2.3. Hallsensor

Ein Hallsensor wird benötigt, um ein Startposition auf der Azimut-Achse zu definieren. Der Halleffekt wurde bereits erklärt. Der gewählte Sensor ist der A1120 und ist ein digitaler Hallsensor (Abbildung 2.21).

Abbildung 2.21: Hallsensor A1120

Das heißt, dass er am Ausgang eine logisch 0 oder 1 ausgibt. Analoge Hallsensoren gibt die Stärke des Magnetfeldes aus. Außerdem ist er unipolar. Wenn ein Magnet mit seiner Südpolseite den Hallsensor annähert, beginnt er sich zu aktivieren. Bei einem Bipolaren braucht es Nord- und Südpol für die Aktivierung. Der Südpol schaltet ihn ein und der Nordpol wieder aus. Der Sensor ist stationär, während das Magnet mit dem Solarpanel dreht. Das Magnet bzw. Solarpanel zeigt bei der Startposition nach Süden. Um Verschaltung zu vereinfachen, wurde ein Modul gemacht. Dabei wurden nur ein Pull-Up-Widerstand und eine Pin-Leiste hinzugefügt (Abbildung 2.22).


Abbildung 2.22: A1120 Modul

# 2.4. Regelungsimplementierung in die Software

Der digitale Regler ist ein ESP32. Mit der Arduino IDE kann der Mikrokontroller programmiert werden. Die Entwickelungsumgebung basiert auf die Programmiersprache C, eine prozedurale und imperative Sprache. Das heißt, dass es die Zeilen nach der Reihenfolge abarbeitet. Ein Arduino-Programm besteht aus zwei Teilen: einem Setup und einem Loop. Im Setup werden alle Zeilen nur einmal ausgeführt und im Loop werden die Zeilen nach dem Durchlauf immer wiederholt.

Abbildung 2.23 zeigt den Zyklus des Regelalgorithmus:

Lohnt sich Regelung?
Azimut: Strommaximum suchen
Schrittmotor zum Maximum ansteuern
Höhenwinkel: Strommaximum suchen
Linearmotor zum Maximum ansteuern
Wenn Azimut 180° gedreht hat, wieder zurückdrehen

Abbildung 2.23: Grafische Darstellung des Algorithmus

Zuallererst stellt sich die Frage, ob sich die Reglung lohnt. Ist die Antwort ja, dann läuft das Programm weiter. Wenn das Gegenteil der Fall ist, bleibt das Programm stehen und misst weiterhin den Strom, bis er groß genug ist. Nach dieser Feststellung wird der Schrittmotor angesteuert und die Mechanik beginnt sich waagrecht zu drehen.

Insgesamt 309 Stunden

# 3. Literaturverzeichnis

Haager, D. D. (2016). Regelungstechnik. Hölder-Pichler-Tempsky GmbH.

# 4. Quellenverzeichnis

Solarzelle – Wikipedia (https://de.wikipedia.org/wiki/Solarzelle)

Solarmodul – Wikipedia (https://de.wikipedia.org/wiki/Solarmodul)

Elektronen-Loch-Paar in der Photovoltaik | PVS Solarstrom (https://photovoltaiksolarstrom.com/photovoltaiklexikon/elektronen-loch-paar/)

Ohne sie geht es nicht: Die Raumladungszone im Kern der Solarzelle (https://photovoltaiksolarstrom.com/photovoltaiklexikon/raumladungszone/)

Photoelektrischer Effekt – Wikipedia (https://de.wikipedia.org/wiki/Photoelektrischer_Effekt)

Messungen an der Solarzelle bei (https://solar.forschendes-lernen.de/wp-content/uploads/sites/12/2012/10/Solarkoffer_Versuche_kurz.pdf)

Lebensdauer einer Solarzelle | EON (https://www.eon.de/de/pk/solar/lebensdauer-solarzelle.html)

ACS712 Stromsensor • Wolles Elektronikkiste (https://wolles-elektronikkiste.de/acs712-stromsensor)

Alles über Hall-Effekt-Sensoren | RS Components | RS Components (https://at.rs-online.com/web/generalDisplay.html?id=ideen-und-tipps/hall-sensoren-leitfaden)

LORENTZ-Kraft | LEIFIphysik (https://www.leifiphysik.de/elektrizitaetslehre/kraft-auf-stromleiter-e-motor/grundwissen/lorentz-kraft)

Shunt Widerstand | Electronics Fundamentals | ROHM (https://www.rohm.de/electronics-basics/resistors/shunt-resistors)

INA219 Strom- und Leistungssensormodul • Wolles Elektronikkiste (https://wolles-elektronikkiste.de/ina219)

INA219 Zerø-Drift, Bidirectional Current/Power Monitor With I2C Interface datasheet (Rev. G) (https://www.ti.com/lit/ds/symlink/ina219.pdf)

https://e2e.ti.com/cfs-file/__key/communityserver-discussions-components-files/6/I2C-Bus-Pullup-Resistor-Calculation.pdf

hall sensor - unterschied unipolar, bipolar, latches - Mikrocontroller.net (https://www.mikrocontroller.net/topic/74847)

A1120LUA-T - Datasheet.Directory (https://datasheet.ciiva.com/26928/a1120lua-t-26928941.pdf)

[^1] (Haager, 2016)
[^2] (Haager, 2016)

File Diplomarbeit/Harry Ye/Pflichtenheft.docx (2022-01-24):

Pflichtenheft

Projektname: S.S.S. - Smart Solar Seeker

Version: 0.3

Datum: 20.10.2021

Version | Datum | Autor | Änderungsgrund/Bemerkungen
0.1 | 29.09.2021 | Harry Ye | Erstellung
0.2 | 05.10.2021 | Harry Ye | Korrigieren nach der Änderung des Lastenheftes
0.3 | 20.10.2021 | Harry Ye | Korrigieren nach Absprache mit Betreuer

# 1 Einleitung

## 1.1 Ziel und Zweck des Dokuments

In diesem Dokument werden alle Anforderungen an den Smart-Solar-Panel beschrieben, die der Auftragnehmer – S.S.S. Diplomarbeitsgruppe – dem Auftragsgeber – Herr Prof. Fuchsberger – für die erfolgreiche Umsetzung des Projektes zu erfüllen hat.

## 1.2 Zweck des Projekts

### 1.2.1 Allgemeines

Durch den photoelektrischen Effekt wandelt eine Photovoltaikzelle Sonnenstrahlung in elektrische Energie um. Der Wirkungsgrad einer Zelle ist unter anderem auch davon abhängig, wie hoch die einfallende Strahlungsenergie ist bzw. von dessen Einstrahlwinkel. Dieses Projekt behandelt eine Nachführung von Photovoltaikzellen, um die Effizienz der Zelle zu erhöhen.

### 1.2.2 Use Case

Ein typisches Anwendungsszenario des Smart-Panels enthält folgende Schritte:

- Das Solarmodul wird von einer Lichtquelle bestrahlt
- Die Sensoren neben dem Panel messen die Lichteinstrahlungen
- Die Messwerte werden zur Steuer- und Regelungssoftware geschickt
- Im Programm werden die Daten verarbeitet
- Die Aktuatoren werden nach der Ausführung der Software gesteuert
- Das Panel wird von der Aktuatorik nachgeführt
- Nach der Nachführung geht das System in Standby
- Nach dem Ablauf einer bestimmten Pausenzeit ist das System im Normalbetrieb

## 1.3 Abkürzungen

S.S.S. → Smart Solar Seeker

## 1.4 Verteiler

Name | E-Mail | Rolle/Bemerkung
Christian Fuchsberger | cfuchsberger@student.tgm.ac.at | Auftraggeber - Betreuer
Wolfgang Baumgartner | wbaumgartner@student.tgm.ac.at | Fachlehrer - Betreuer
Edis Kereku | ekereku@student.tgm.ac.at | Projektleiter bei Auftragnehmer
Steven Dudek | sdudek@student.tgm.ac.at | Entwickler bei Auftragnehmer
Halil Senel | hsenel@student.tgm.ac.at | Entwickler bei Auftragnehmer
Harry Ye | hye@student.tgm.ac.at | Entwickler bei Auftragnehmer

## 1.5 Projektteams und Schnittstellen

Das Entwicklungsteam beim Auftragnehmer besteht aus den folgenden Personen:

Name | E-Mail | Rolle/Bemerkung
Edis Kereku | ekereku@student.tgm.ac.at | Projektleiter bei Auftragnehmer
Steven Dudek | sdudek@student.tgm.ac.at | Entwickler bei Auftragnehmer
Halil Senel | hsenel@student.tgm.ac.at | Entwickler bei Auftragnehmer
Harry Ye | hye@student.tgm.ac.at | Entwickler bei Auftragnehmer

## 1.6 Zeitdauer

Das Projekt muss bis 5. April 2022 fertiggestellt sein. Erstellung des Pflichtenhefts am 29. September 2021. Zeit bis zur Fertigstellung: ca. 6 Monate.

# 2 Anforderungsbeschreibung

## 2.1 Anforderung 1 – Mechanik

### 2.1.1 Beschreibung

Für das 8kg schwere Solarpanel soll ein passendes Gestell konstruiert werden, welches gegen Wettereinflüsse und physikalische Einwirkungen standhaft sein soll. Dabei werden Holz und Aluminium verwendet. Im Hohlraum der Grundplattform soll die Elektronik montiert werden. Die Plattform wird mit Holzplatten umhüllt, damit die Elektronik geschützt ist. Gehalten wird das Solarpanel mit einer beweglich gelagerten Stange, die mit einem Zahnrad bewegt wird. Ein Schrittmotor treibt das Zahnrad an. Die mittige Stange soll maximal 10kg halten können, Solarpanel plus die angebrachte Stange am Solarpanel. Zwischen dieser Stange und dem Solarpanel ist ein Drehgelenk montiert, um den Winkel des Panels mit dem Linearmotor zu verändern. Ein Verlegeplan wird gezeichnet, damit bei einem Fehlerfall während der Nachstellung die Elektronik und die Kabeln nicht beschädigt werden. Nach dem Zusammenbau wird mit Kräfteeinwirkungen eines Menschen auf Belastbarkeit überprüft.

### 2.1.2 Zeitdauer

Wahl der mechanischen Bauteile: 20 Personenstunden

Konstruktion und Entwickelung der Mechanik: 50 Personenstunden

Verarbeitung und Zusammenbau der Mechanik: 80 Personenstunden

Testen auf Belastbarkeit und Stabilität der Mechanik: 20 Personenstunden

Gesamtaufwand: 200 Personenstunden

Gesamtdauer: 4 Monate

## 2.2 Anforderung 2 – Regelung

### 2.2.1 Beschreibung

Als Lichtsensor wird ein Miniaturpanel verwendet, der wird neben dem größeren Panel befestigt. Um die Werte des Minipanels zu messen, wird der IC INA219 verwendet. Er wandelt die Werte, die an einem Shuntwiderstand anliegen, in Spannungen um, damit der Mikrokontroller sie einlesen und auswerten kann. Zuerst liest der Mikrokontroller mehrere Werte des ICs ein. Falls sie zu niedrig sind, ist der jetzige Wetterzustand bewölkt und es wird nicht nachgeführt. Wenn die Werte hoch genug sind, folgt das Panel in Azimut-Richtung den Sonnenverlauf aus dem Internet, bis ein Höchstwert erzielt wird. Um diesen Wert zu kriegen, werden so lange Werte eingelesen, bis der vorherige Wert größer ist als der Nächste. Dann wird zurück auf die Position gedreht, wo der Höchstwert eingelesen wurde. Nach dem Einstellen des Azimuts wird der Höhenwinkel des Panels geregelt. Das Prinzip bleibt gleich. Somit folgt zuerst das Panel den Sonnenverlauf, der vom Mikrokontroller aus der Webseite geholt wurde, danach sucht sich der Mikrokontroller die beste Position für die Nachführung aus. Um das Gerüst zu bewegen, müssen die Motoren angesteuert werden. Dies wird mit dem Zusammenspiel der zwei H-Brücken, des Mikrokontrollers und der Motoren erreicht. Die Software steuert die H-Brücken so an, dass die Nachführung rechtzeitig und effizient verläuft. Nach der Regelung geht der Mikrokontroller in Standby und somit auch das System. Die Leistung des Prozesses muss gemessen werden. Um die übrige Leistung herauszufinden, wird die gemessenen Leistung mit der Eingangsleistung verglichen.

### 2.2.2 Zeitdauer

Auswahl der Sensorik: 10 Personenstunden

Überlegung der Regelung: 10 Personenstunden

Realisierung der Regelung: 30 Personenstunden

Messen des Systems: 20 Personenstunden

Gesamtaufwand: 70 Personenstunden

Gesamtdauer: 2 Monate

## 2.3 Anforderung 3 – Entwickelung der Hardware

### 2.3.1 Beschreibung

Der Ausgang des Panels wird mit einem Laderegler bzw. Solarkontroller angeschlossen. Außerdem ist eine 12V Batterie und der Verbraucher, also die ganze Hardware, mitangeschlossen. Der Kontroller senkt die Spannung des Solarpanels von 18V auf 12V, damit die Batterie aufgeladen werden kann. Somit agieren das Solarpanel und die Batterie, falls das Panel zu wenig Leistung liefert, als Versorger. Am Verbraucheranschluss des Kontrollers wird die ganze Hardware mit 24V versorgt. Da die Spannung für die meisten Komponenten zu hoch ist, kommen zwei Step-Down-Converter bzw. Abwärtswandler ins Spiel. Eines versorgt den ESP32 mit 3,3V und das andere die H-Brücken mit 5V. Die beiden H-Brücken versorgen und steuern die zwei Motoren an. Es gibt eine logische Versorgung 5V für die Ansteuerung und eine externe Versorgung 24V für die Motoren. Die Steuerung der Brücken macht der Mikrokontroller. Das heißt, dass die Schwierigkeit in der Kommunikation zwischen den zwei Bauteilen liegt. Wenn alle Hardwarekomponenten fertig und einsatzbereit sind, wird ein Entwicklerboard gefertigt, auf dem wird die ganze Hardware bestückt und miteinander verbunden.

### 2.3.2 Zeitdauer

Auswahl des Lagereglers: 10 Personenstunden

Entwickelung der H-Brücken: 60 Personenstunden

Entwickelung der Abwärtswandler: 60 Personenstunden

Entwickelung des Entwicklerboards: 60 Personenstunden

Gesamtaufwand: 190 Personenstunden

Gesamtdauer: 4 Monate

## 2.4 Anforderung 4 – Software

### 2.4.1 Beschreibung

Die Software ist das Gehirn des Systems. Sie ist im Mikrokontroller gespeichert. Zuerst liest der Mikrokontroller die derzeitigen Koordinaten aus dem Positionssensors. Daraus folgt das Herausholen des jetzigen Sonnenverlaufes aus dem Internet. Vor der Nachführung wird vom Stromsensor die Werte des Miniaturpanels eingelesen, um zu bestimmen, ob die Nachführung sich lohnt. Wenn es sich lohnt, werden die Motoren mit den herausgefundenen Längen- und Breitengrad der Sonne gesteuert. Mit den Werten des Stromsensors wird das Panel nachgeregelt, um die Nachführung genauer zu machen. Nach der Nachführung geht der Mikrokontroller in Standby, um Energie zu sparen. Nach einer Stunde startet die Regelung von neu. Dafür wird im Programm ein Timer geschrieben. Außerdem wird ein Fail-Safe Zustand eingebaut, damit bei einem Ausfall des Systems das Panel in eine Ruhelage ist.

### 2.4.2 Zeitdauer

Programmieren der Software: 90 Personenstunden

Testen der Software: 10 Personenstunden

Gesamtaufwand: 100 Personenstunden

Gesamtdauer: 2 Monate

## 2.5 Anforderung 5 – Verbraucher

### 2.5.1 Beschreibung

Mit der ausreichenden Energie sollen mindestens fünf Handys aufgeladen werden. Die Handys werden am Solarkontroller angeschlossen und aufgeladen. Dazu wird der Batteriestand auf dem Display angezeigt, der wiederum vom Mikrokontroller gesteuert wird.

### 2.5.2 Zeitdauer

Programmieren der Funktion: 10 Personenstunden

Gesamtaufwand: 10 Personenstunden

Gesamtdauer: 1 Tag

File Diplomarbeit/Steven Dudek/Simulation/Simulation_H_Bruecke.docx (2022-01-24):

Aufbau der Schaltung:


Das einzige was verändert wird sind die Zustände

Zustände:


1. Zustand (Vorne beschleunigen):


3 Zustand(Rückwärts beschleunigen)::


2 Zustand(Vorne bremse)::

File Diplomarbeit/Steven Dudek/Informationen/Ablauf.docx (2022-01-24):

Ablauf:

Solarpanel messung

Datenblatt h-brücke

h-brücke simulation

h-brücke mit mosfet

h-brücke als modul

datenblatt stepdown

Dimensionierung step down

simulation von step down

step down schaltungen

step down nachgemessen

step down fehler bei 5V

spannungsregler bei usb ports

Schraubklemmen verwenden

Doku, protokoll, betreungsprotokoll

Entwicklerboard

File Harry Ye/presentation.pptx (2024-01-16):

## Regelung

SPSP – Smart Photovoltaik Solar Panel
Harry Ye
(Entwurf und Implementierung des Regelungsverfahrens, Test und Inbetriebnahme des Prototyps)

## Regelkreis


## Regelzyklus

Strommessungen des kleinen Solarpanels
Lohnt sich die Regelung?
Höhen-Regelung
Azimut-Regelung
1h Pause

- Bis sich um 180° gedreht wurde
- Nullpunktposition

## Nullpunktposition


## Höhen-Regelung


Sucht Maximum
Pro 0.1s eine Messung
Fährt zur Ausgangposition
Fährt zum Maximum
Nullpunktposition


## Azimut-Regelung


Sucht Maximum
Dreht sich zum Maximum
Dreht sich zur Ausgangposition
Pro Schritt eine Messung
Nullpunktposition


## Nach Kalibrierung


## Vielen Dank für Ihre Aufmerksamkeit

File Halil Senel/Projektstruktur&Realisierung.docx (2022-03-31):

# Projektstruktur

Rolle(n) | Name | E-Mail
Projektbetreuer SPSP (Hauptverantwortlich) | Dipl. Ing. Christian Fuchsberger | cfuchsberger@tgm.ac.at
Projektbetreuer SPSP | Ing. Wolfgang Baumgartner | wbaumgartner@tgm.ac.at
Teamleiter SPSP | Kereku Edis | ekereku@student.tgm.ac.at
Teammitglied SPSP | Dudek Steven | sdudek@student.tgm.ac.at
Teammitglied SPSP | Ye Harry | hye@student.tgm.ac.at
Teammitglied SPSP | Senel Halil | hsenel@student.tgm.ac.at

Tabelle 1 Struktur Personal SPSP

Behandelte Arbeitsbereiche der Teammitglieder (teilweise wurde über die individuellen Themenstellungen hinaus in weiteren Bereichen des Projekts mitgewirkt bzw. mitgeholfen):

Kereku:

- Projektleitung
- Softwareentwicklung
- Softwareintegration

Dudek:

- Hardwareentwicklung
- Schaltungsentwicklung und PCB-Design der Platine

Ye:

- Regelungsentwicklung
- Softwareentwicklung
- Softwareintegration

Senel:

- Mechanische Entwicklung
- Technische Zeichnung

# Mechanische Entwicklung (Senel)

mechanische Entwicklung
Überlegungen
Skizze
Realisierung
3D-Modell
technische Zeichnung

Abbildung 1 Gliederung der Mechanischen Entwicklung

Zuerst wurde festgelegt welches Ziel bzw. welche Funktion der mechanische Aufbau haben soll. Nach der Festsetzung der Ziele wurde eine grobe Skizze gezeichnet. Danach wurde die Mechanik aufgebaut und anschließend ein 3D-Modell erstellt. Zum Schluss wurden die technischen Zeichnungen entworfen.

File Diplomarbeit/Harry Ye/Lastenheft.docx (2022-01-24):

Lastenheft

Projektname: S.S.S. – Smart Solar Seeker

Version: 0.3

Datum: 20.10.2021

Version | Datum | Autor | Änderungsgrund/Bemerkungen
0.1 | 21.09.2021 | Harry Ye | Erstellung
0.2 | 30.09.2021 | Harry Ye | Korrigieren nach der Kontrolle des Betreuers
0.3 | 20.10.2021 | Harry Ye | Nach Bearbeiten des Pflichtenhefts

Inhaltsverzeichnis

# 1 Einleitung

## 1.1 Ziel und Zweck des Dokuments

In diesem Dokument werden die Anforderungen an das Smart-Panel beschrieben, die der Auftraggeber Professor Fuchsberger für die erfolgreiche Umsetzung des Projekts an den Auftragnehmer stellt.

## 1.2 Zweck des Projekts

### 1.2.1 Allgemeines

Durch den photoelektrischen Effekt wandelt eine Photovoltaikzelle Sonnenstrahlung in elektrische Energie um. Der Wirkungsgrad einer Zelle ist unter anderem auch davon abhängig, wie hoch die einfallende Strahlungsenergie ist bzw. von dessen Einstrahlwinkel. Dieses Projekt behandelt eine Nachführung von Photovoltaikzellen, um die Effizienz der Zelle zu erhöhen.

### 1.2.2 Use Case

Ein typisches Anwendungsszenario des Smart-Panels enthält folgende Schritte:

- Das Solarmodul wird von einer Lichtquelle bestrahlt
- Die Lichtsensoren neben dem Panel messen die Lichteinstrahlungen
- Die Messwerte der Lichtsensoren werden zur Steuer- und Regelungssoftware geschickt
- Der Positionssensor liefert die Information des Sonnenverlaufes aus dem Internet an den Mikrocontroller
- Das Programm verarbeitet die Messwerte und die Daten aus dem Internet, um die bestmögliche Position zu erhalten
- Die Aktuatoren werden nach der Ausführung der Software geregelt
- Das Panel wird von der Aktuatorik nachgeführt
- Nach der Nachführung geht das System in Standby
- Nach dem Ablauf einer bestimmten Pausenzeit startet die Regelung von neu

## 1.3 Abkürzungen

S.S.S. → Smart Solar Seeker

## 1.4 Verteiler

Dieses Dokument wird nach Anforderung an folgende Personen per E-Mail übermittelt.

Name | E-Mail | Rolle/Bemerkung
Christian Fuchsberger | cfuchsberger@tgm.ac.at | Auftraggeber – Projektbetreuer
Wolfgang Baumgartner | wbaumgartner@tgm.ac.at | Fachlehrer – Projektbetreuer

# 2 Anforderungsbeschreibung

## 2.1 Anforderung 1 – Mechanik

Für das 8kg schwere Solarpanel soll ein passendes Gerüst konstruiert werden, welches gegen Wettereinflüsse und physikalische Einwirkungen standhaft sein soll. Außerdem soll das Gerüst, während das Panel sich bewegt, stabil sein.

## 2.2 Anforderung 2 – Regelung

Ein Lichtsensor misst den aktuellen Strom der Sonneneinstrahlung. Der Mikrokontroller verarbeitet die Messungen, damit die Aktuatorik und somit auch das Solarpanel richtig geregelt werden.

## 2.3 Anforderung 3 – Entwickelung der Hardware

Damit alle Komponenten im System versorgt und miteinander verbunden sind, muss dementsprechend eine Hardware dafür entwickelt werden. Sie kümmert sich um das Entwicklerboard, das alle Bauteile enthält.

## 2.4 Anforderung 4 – Software

Die Software ist das Gehirn des Systems und steuert somit die Sensorik und Aktuatorik. Auch der ganze Nachführprozess wird erst durch die Software ermöglicht. Sie ist im Mikrokontroller gespeichert.

## 2.5 Anforderung 5 – Verbraucher

Nachdem die ganze Hardware mit der Sonnenenergie versorgt wurde, soll mit der übrigen Energie fünf Handys aufgeladen werden.

Version: 0.3 Smart Solar Seeker 20.10.2021

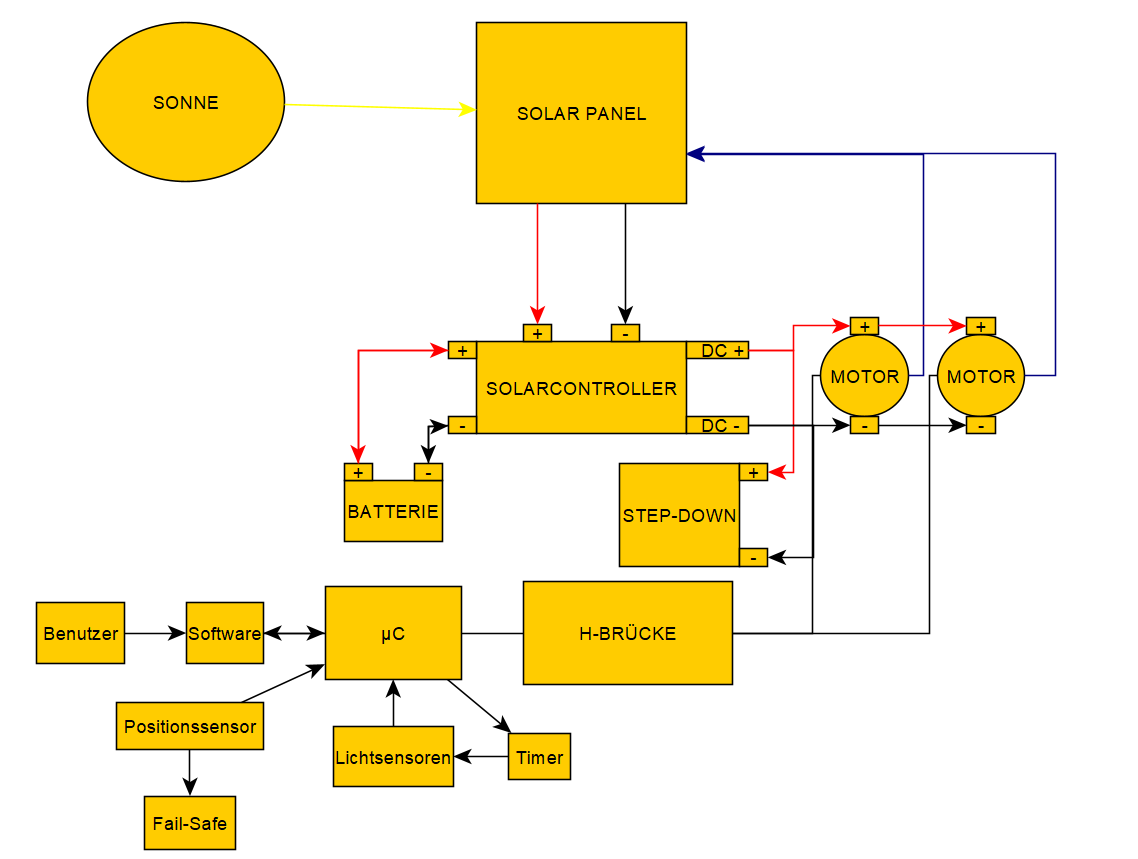
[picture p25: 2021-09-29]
Allgemein/Blockschaltbild.v2.png

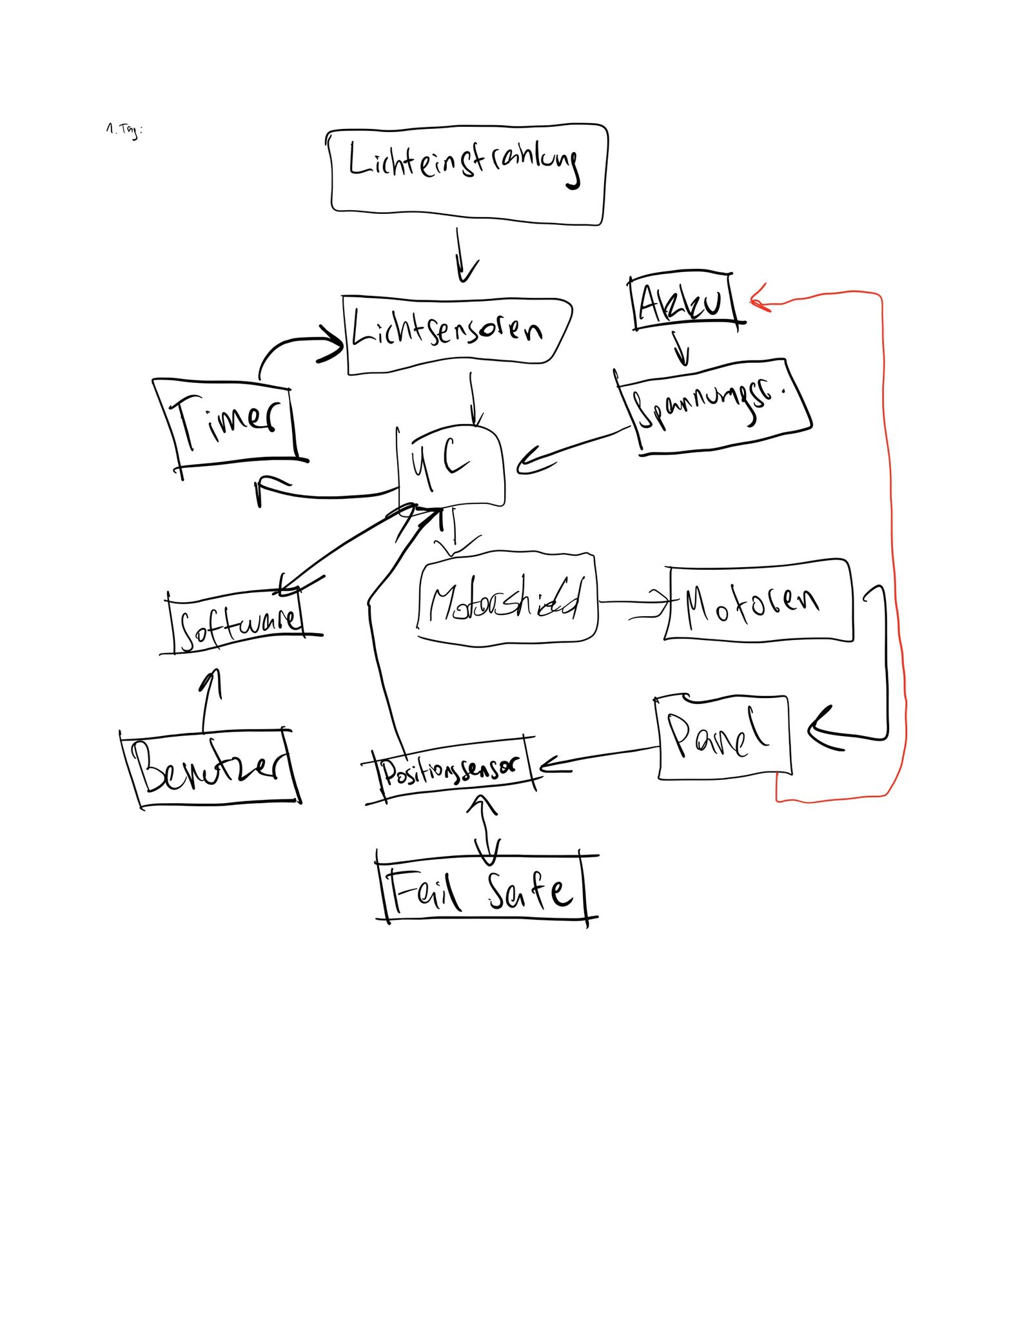
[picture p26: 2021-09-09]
Steven Dudek/Blockschaltbild_v1.jpg

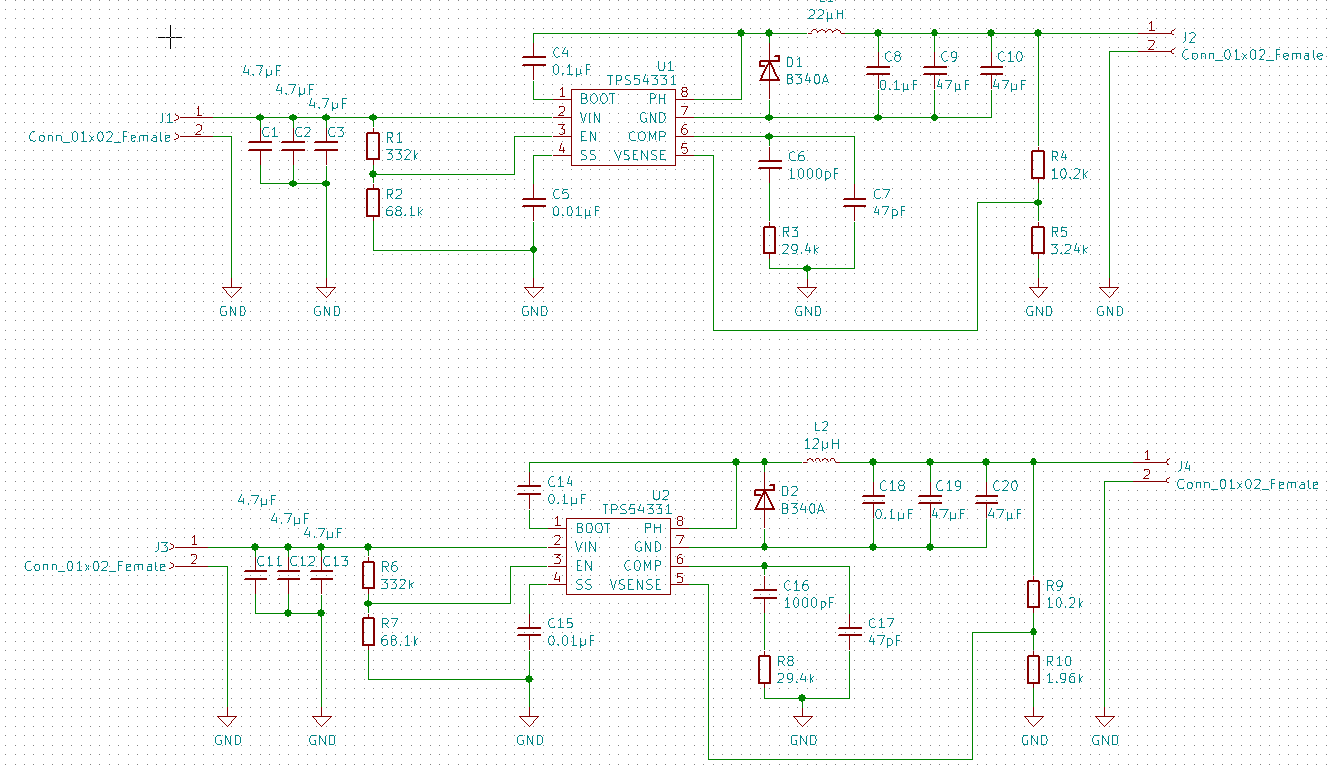
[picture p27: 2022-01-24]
Steven Dudek/Layout/Scematic_von_3_3_und_5V.PNG

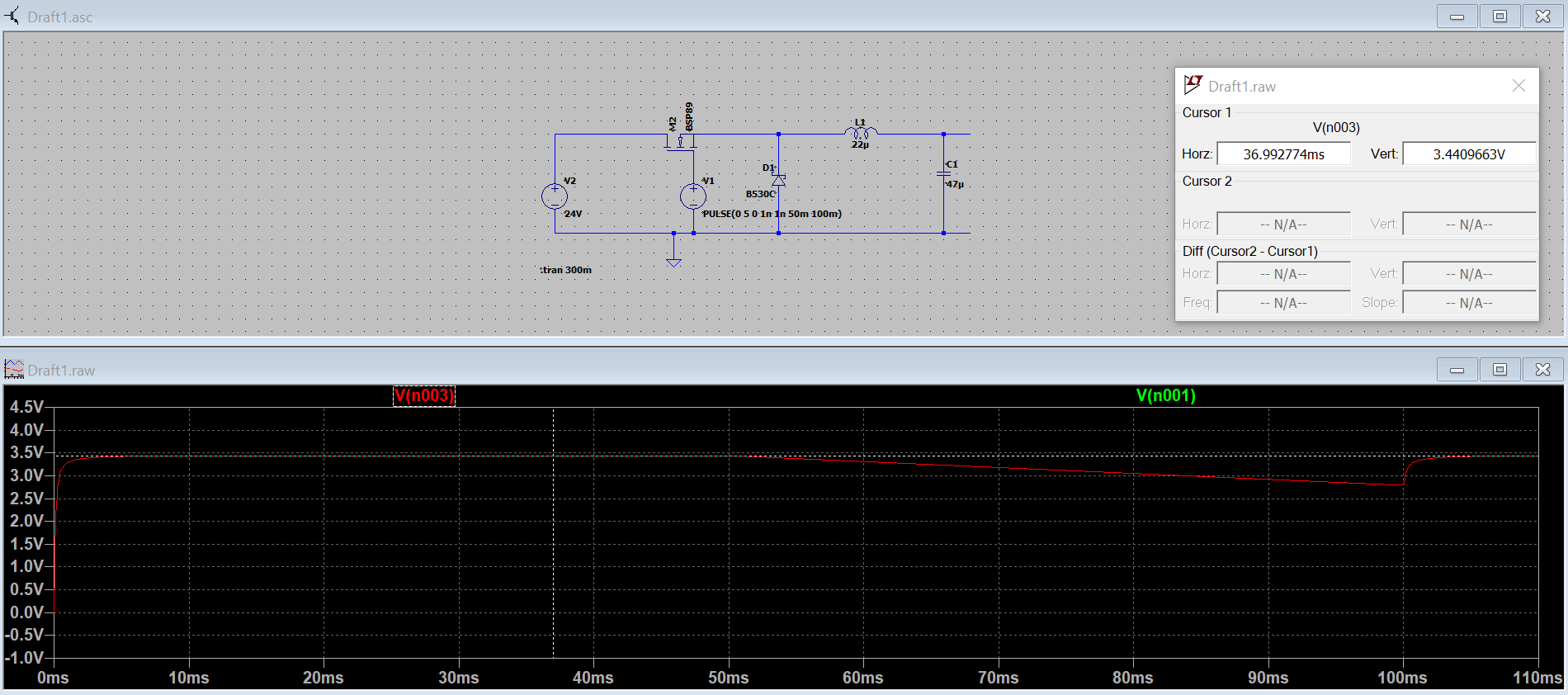
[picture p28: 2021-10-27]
Diplomarbeit/Steven Dudek/Simulation/Simulation_Stepdown_24auf3_3V.PNG

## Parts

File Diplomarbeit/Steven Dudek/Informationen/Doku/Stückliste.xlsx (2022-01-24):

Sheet: Tabelle1
Stückliste Step-Down SSS v1:
Bauteil: | Bauteilwert: | Bestellnummer (RS): |  | Stück:
Speicherdrossel | 22uH | 874-9784 |  | wenn möglich 2
B340A Shottky | / | 146-4773 | eventl. Alternative suchen | leider 100 Stück nur möglich
Speicherdrossel | 12uH | 432-4439 |  | 1
DC-DC-Wandler | / | 661-8521 |  | 3
Alternativ:
b340b Shottky | / | 738-4787

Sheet: Tabelle2
Stückliste Step-Down SSS v2:
Bauteil: | Bauteilwert: | Bestellnummer (RS): |  |  | Stück:
Speicherdrossel | 22uH | 874-9784 | ü | izzda | 2
Speicherdrossel | 12uH | 432-4439 | ü | izzda | 2
DC-DC-Wandler | / | 661-8521 | ü | izzda | 5
Kondensator | 4,7µF | 133-5646 | ü | izzda | 25
Kondensator | 47pF | 378-681 | ü | izzda | 25
Kondensator | 47µF | 215-8439 | ü | izzda | 10
Widerstand | 29,4kOhm | 215-4058 | ü | izzda | 10
Widerstand | 3,24kOhm | 197-8309 | ü | izzda | 100
Widerstand | 2kOhm | 901-3727 | ü | izzda | 100

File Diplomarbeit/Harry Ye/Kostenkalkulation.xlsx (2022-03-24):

 |  | Teilnehmer |  | Jahrgang |  | Kosten unter Annahme eines privatwirtschaftlichen Umfeldes
 |  | Dudek, Kereku, Senel, Ye |  | 5AHEL
Kalkulation-Entwicklungskosten |  |  |  |  |  | im Rahmen eines Dienstverhältnisses |  | auf Basis Werk-Vertrag
 |  |  |  |  |  | Planung | Realisierung
KOSTENARTEN |  |  |  | Ist-Daten Stand: | 2021-12-21 08:19 | SOLLKOSTEN | ISTKOSTEN | ISTKOSTEN
 |  |  |  | Plan-Daten Stand: | 2021-10-28 | Aktualisiert
Material-Einzelkosten exklusive Ust. |  |  | Rechnung [€]
 | Elektronische Bauteile |  | 75.00 |  |  | 75.00 | 75.00 | 75.00
 | Mechanische Bauteile |  | 50.00 |  |  | 50.00 | 50.00 | 50.00
 | Autobatterie |  | 100.00 |  |  | 100.00 | 100.00 | 100.00
 | Motoren |  | 200.00 |  |  | 200.00 | 200.00 | 200.00
 | Solarpanel |  | 200.00 |  |  | 200.00 | 200.00 | 200.00
 | Materialgemeinkostenzuschlag |  |  |  | 18.00% | 112.50 | 112.50
Einzelmaterial-Kosten Summe |  |  |  |  |  | 737.50 | 737.50 | 625.00
Verwendete Geräte exklusive Ust. |  | AW > 399 € | Menge [h] | Neupreis [€] | Nutzungs-Dauer [h]
 | Spezialnetzgerät |  | 100 | 500.00 | 87660 | 0.57 | 0.57
 | Multimeter |  | 50 | 50.00 | 43800 | 0.06 | 0.06
 | Lötkolben-Station |  | 50 | 150.00 | 87600 | 0.09 | 0.09
 | HF-Oszilloskop |  | 100 | 9000.00 | 43830 | 20.53 | 20.53
 | Bohrmaschine |  | 20 | 410.00 | 8766 | 0.94 | 0.94
 | Ätzanlage |  | 10 | 10000.00 | 17532 | 5.70 | 5.70
 | Lenovo Yoga |  | 300 | 500.00 | 43800 | 3.42 | 3.42
 | Lenovo Thinkpad |  | 300 | 583.00 | 43800 | 3.99 | 3.99
 | Apple Ipad |  | 300 | 416.00 | 8760 | 14.25 | 14.25
 | Microsoft Surface 3 |  | 300 | 416.00 | 35040 | 3.56 | 3.56
 | Lenovo Ideapad 300 |  | 300 | 666.00 | 61320 | 3.26 | 3.26
Kalk.Afa-Kosten Summe |  |  |  |  |  | 56.37 | 56.37
SW/Lizenzen/Gebühren exklusive Ust. |  |  | Ankauf für Projekt [Neupreis €] | Nutzung [%] | Schul-SW-Lizenz [€/Jahr]
 | MATLAB |  | 2000.00 |  |  | 2000.00 | 2000.00 | 2000.00
 | Microsoft Office 365 |  |  | 60% | 100.00 | 60.00 | 60.00 | 60.00
SW/Lizenz/Gebühren-Kosten Summe |  |  |  |  |  | 2060.00 | 2060.00 | 2060.00
Raum-/Energie-Kosten exklusive Ust. |  |  | Menge [h] | [m2] | Kosten/m2 pro Monat
 | Labor |  | 200 | 50.00 | 25.00 | 347.22 | 347.22
 | Werkstatt |  | 100 | 100.00 | 15.00 | 208.33 | 208.33
Raum/Energie-Kosten Summe |  |  |  |  |  | 555.56 | 555.56
Personalkosten exklusive Ust. |  | Monatsgehalt [€] | Menge [h] | Stunden-Kosten [€] | Stunden-Satz Werkvertrag
 | ProjektleiterIn | 5000.00 | 300 | 29.99 | 100.00 | 8997.93 | 8997.93 | 30000.00
 | EntwicklerIn | 3000.00 | 300 | 18.00 | 60.00 | 5398.76 | 5398.76 | 18000.00
 | EntwicklerIn | 3000.00 | 300 | 18.00 | 60.00 | 5398.76 | 5398.76 | 18000.00
 | EntwicklerIn | 3000.00 | 300 | 18.00 | 60.00 | 5398.76 | 5398.76 | 18000.00
 | Personalgemeinkostenzuschlag |  |  |  | 120.00% | 30233.05 | 30233.05
 |  |  | Rechnung [€] | gefahrene Km | Amtl. Km-Geld [€]
 | Reisekosten (Top-Jugendticket) |  | 316.00 |  |  | 316.00 | 316.00 | 316.00
Personal-Kosten Summe |  |  |  |  |  | 55743.25 | 55743.25 | 84316.00
Vertrieb-Einzelkosten exklusive Ust. |  |  | Rechnung [€] | Kosten [€/Stk] | [Stk.]
 | A4-Buch |  |  | 19.20 | 1 | 19.20 | 19.20 | 19.20
 | A4-Papier |  |  | 0.05 | 100 | 5.00 | 5.00 | 5.00
Vertriebs-Einzelkosten Summe |  |  |  |  |  | 24.20 | 24.20 | 24.20
Projekt Gesamt-Herstellungskosten |  |  |  |  |  | 59176.88 | 59176.88 | 87025.20
 | Verwaltungsgemeinkostenzuschlag |  |  |  | 9.00% | 5325.92 | 5325.92
 | Vertriebsgemeinkostenzuschlag |  |  |  | 5.00% | 2958.84 | 2958.84
Projekt Entwicklungs-Selbstkosten |  |  |  |  |  | 67461.64 | 67461.64 | 87025.20
Kalkulation für die Kleinserie |  |  |  |  |  | Kosten im privatwirtschaftlichen Umfeld
 |  |  |  |  |  | im Rahmen eines Dienstverhältnisses |  | auf Basis Werk-Vertrag
 |  |  |  |  |  | Planung | Realisierung
Stückzahl - Kleinserie |  |  |  | 100 | Stk. | SOLLKOSTEN | ISTKOSTEN | ISTKOSTEN
 |  |  |  |  |  | Aktualisiert
Entwicklungskosten |  |  |  |  |  | 67461.64 | 67461.64 | 87025.20
Materialkosten (-20 % Mengenrabatt) |  |  |  |  |  | 59000.00 | 59000.00 | 50000.00
Personalkosten (inkl. Gemeinkosten) |  |  |  | 10.00 | h/Stk. | 39590.89 | 39590.89 | 60000.00
Raumkosten |  |  |  |  |  | 2083.33 | 2083.33
Maschinen/Gerätekostenpauschale |  |  |  | €1.00 | /Stk. | 100.00 | 100.00
Gesamt-Herstellungskosten Kleinserie |  |  |  |  |  | 168235.87 | 168235.87 | 197025.20
Herstellungskosten/Stück |  |  |  |  |  | 1682.36 | 1682.36 | 1970.25
Verwaltungsgemeinkostenzuschlag |  |  |  |  | 9.00% | 151.41 | 151.41 | 177.32
Vertriebsgemeinkostenzuschlag |  |  |  |  | 5.00% | 84.12 | 84.12 | 98.51
Selbstkosten €/Stück |  |  |  |  |  | 1917.89 | 1917.89 | 2246.09
Gewinnzuschlag-IST |  |  |  |  | 5.00% |  | 95.89 | 112.30
Gewinnzuschlag-SOLL |  |  |  |  | 15.00% | 287.68
Netto-Verkaufspreis €/Stk |  |  |  |  |  | 2205.57 | 2013.78 | 2358.39
 | + Ust |  |  |  | 20.00% | 441.11 | 402.76 | 471.68
Brutto-Verkaufspreis €/Stk |  |  |  |  |  | 2646.69 | 2416.54 | 2830.07
 | Die Projektkalkulation ist integraler Bestandteil der Projektmappe. Ich empfehle pro Projektgruppe eine/n Verantwortliche/n zu definieren. Die Vorkalkulation (Sollkosten) ist gruppenweise mit Ende der Herbstferien per mail an den Wirtschaftslehrer abzugeben. Die Endkalkulation (Istkosten) ist bis spätestens 1 Woche vor Notenschluss am Ende des Schuljahres per mail abzugeben. Für nicht abgegebene Kalkulationen ist die gesamte Projektgruppe verantwortlich. Das Grundprinzip dieser Kalkulation besteht darin, dass eine realwirtschaftliche Situation simuliert wird. Damit gibt es KEINE kostenlosen Leistungen von Seiten der Schule - ALLES ist kostenmäßig zu erfassen/ermitteln/schätzen.

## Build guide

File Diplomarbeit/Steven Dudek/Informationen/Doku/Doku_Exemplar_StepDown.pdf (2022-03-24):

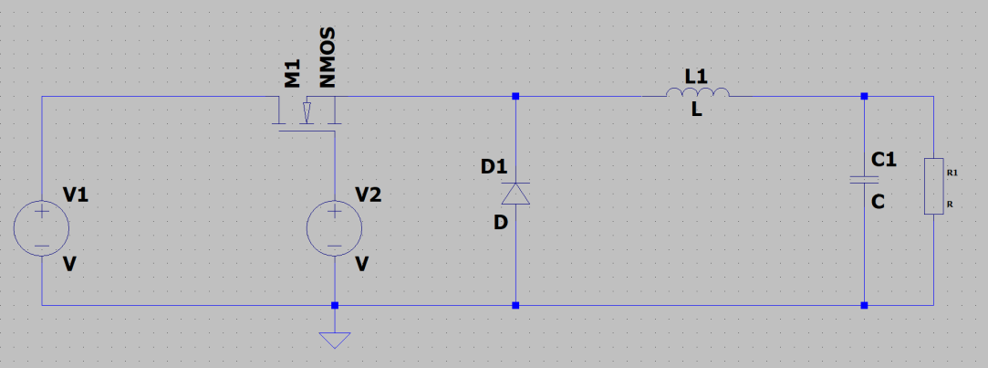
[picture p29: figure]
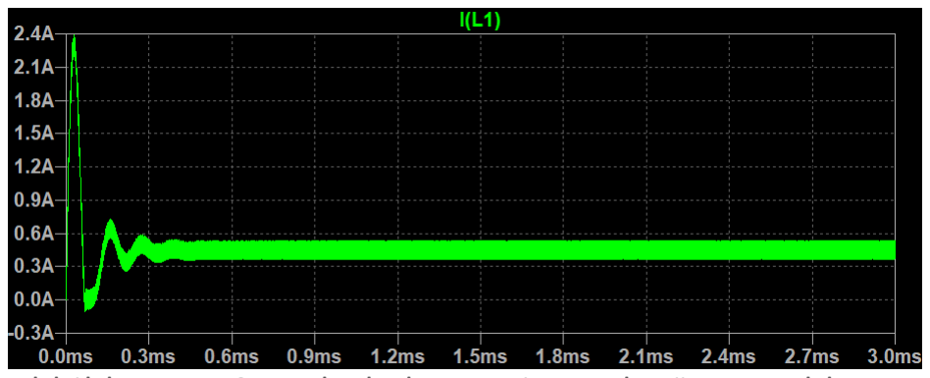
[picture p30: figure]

1Quelle: http://schmidt-walter-schaltnetzteile.de/snt/snt_deu/sntdeu2.pdf 2 Quelle: https://de.wikipedia.org/wiki/Abw%C3%A4rtswandler
3 Quelle: https://de.wikipedia.org/wiki/Abw%C3%A4rtswandler

## 1. DC-DC-Wandler (Abwärtswandler)

Der Abwärtswandler (auf Englisch: Buck-Converter, Step-down-Converter) wandelt eine Eingangsspannung in eine niedrigere Ausgangsspannung. Er wird auch Tiefsetzsteller genannt.¹

Abbildung 1: Grundschaltung eines Abwärtswanlder

## 1.1 Funktion

Der Schalter (bei uns ein NMOSFET) wird mit einer Spannungsgesteuerten Quelle ein- und ausgeschaltet. Üblicherweise werden reichen die Schaltzyklen von einigen Stück bis mehrere Millionen pro Sekunde. Es unterscheiden sich 2 Phasen bei der Schaltung. Im geöffneten Zustand ermöglichen die beiden Energiespeicher Spule und Kondensator die Versorgung an der Last. Die Größe des Ausgangsignals kann mithilfe der Schaltzeit, Größe des Steuersignals, Größe des Eingangssignal und die Größe der Induktivität und Kapazität eingestellt werden.

Während der Einschaltzeit Te fließt der Laststrom durch die Spule L und durch den Verbraucher; die Diode D sperrt. Während der Ausschaltphase Ta wird die in der Spule gespeicherte Energie abgebaut: Der Strom durch den Verbraucher fließt weiter, nun jedoch durch die Diode D und aus dem Kondensator C.² Die Spule und der Kondensator bilden einen Tiefpass zweiter Ordnung. Die Abwärtswandlung wird dadurch erreicht, dass der Wechselanteil des Rechtecksignals rausgefiltert wird und nur noch die Gleichspannung vorhanden ist. Die Gleichspannung wird mit dem Tastverhältnis eingestellt.

## 1.2 Lückender und nichtlückender Betrieb

Nichtlückender Betrieb (kontinuierlicher Betrieb): Der Strom, der durch die Spule fließt, hört
während des gesamten Zyklus nie auf zu fließen. Der Schalter wird, bevor die magnetische Energie an der Spule vollständig abgebaut ist, geschlossen.

Abbildung 1: Grundschaltung eines Abwärtswanlder

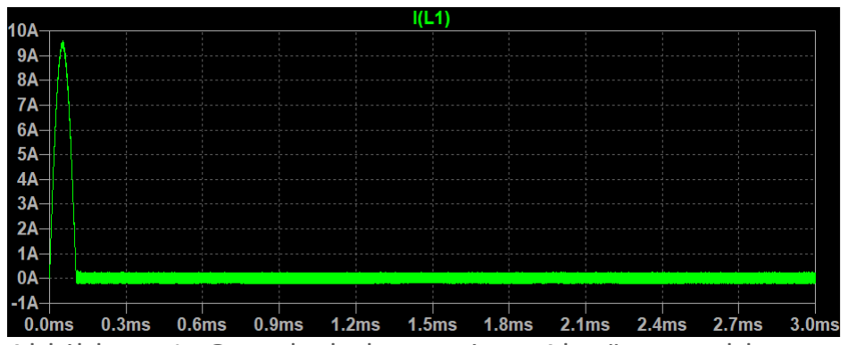
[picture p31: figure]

1Quelle: http://schmidt-walter-schaltnetzteile.de/snt/snt_deu/sntdeu2.pdf 2 Quelle: https://de.wikipedia.org/wiki/Abw%C3%A4rtswandler

Lückender Betrieb: Der Strom, der durch die Spule fließt, fällt nach jedem Zyklus auf null. Bei der Energiefreisetzung kommt die Lück-Phase ohne Strom durch die Spule. Die angeschlossene Last wird nur noch über den Kondensator versorgt.

Abbildung 1: Grundschaltung eines Abwärtswanlder

Die Veränderung auf lückenden auf nichtlückender oder nichtlückender und lückender Betrieb, hängt von von der Induktivität, Eingangsspanung, Ausgangsspannung, Schalfrequenz und des Ausgangstromes ab. Die Betriebsarten unterscheiden sich von der Steuerkennlinie (Abhängigkeit von der Ausgangsspannung zum Tastgrad) und die Störstrahlung (EMV)

## 1.3 Regelung und Steuerung

Es gibt verschieden Verfahren für die Regelung der Ausggangsspannung. In unserem Fall ist es die Pulsweitenmodulation im nichtlückenden Betrieb.

## 1.3.1 Strom- und Spannungsverlauf

Der Strom in der Spule pendelt mit einem Segelzahnverlauf um den Mittelwert. Dieser sinkt dabei nie auf Null ab. Die Ausgangsspannung wird über den Zeitraum der Periodendauer als konstant angesehen.

Der Spulestrom beträgt: iL ∫ uLdt + I0

Während der Einschaltphase wird die Spule geladen. Der Strom in der Spule steigt linear an. Die Spannung in der Spule beträgt während der Einschaltphase die Differenz von Eingangs- und Ausgangsspannung.

uL = Ue − Ua

In der Ausschaltphase beträgt die Spannung an der Spule: UL = −Ua

Der Vorgang wiederholt sich in Abhängigkeit von der Periodendauer. Der Gleichstromanteil der Spule (I0) wird als Biasstrom bezeichnet und darf die Spule nicht sättigen. Der Wechselstromanteil der Spule wird auch als Rippelstrom bezeichnet.

Am Knotenpunkt von Schalter, Diode und Spule zeigen die Ergebnisse große Spannungssprünge auf. Dieser Knotenpunkt soll im PCB-Layout möglichst kurz sein.

Der Tastgrad d, wenn ungeformt, beträgt: d =

UA
UE

1Quelle: http://schmidt-walter-schaltnetzteile.de/snt/snt_deu/sntdeu2.pdf 2 Quelle: https://de.wikipedia.org/wiki/Abw%C3%A4rtswandler

## 1.4 Verlustleistung

Der reale Step-down-Converter hat seine Verlustleistung in den integrierten Bauteilen. Diese Bauteile sind:

- Schaltransistor – Spannungsabfall im eingeschalteten Zustand und Schaltverluste
- Spule – ohmsche (Wicklungswiderstand) und magnetische (Kernmaterial) Verluste
- Freilaufdiode – Flussspannung (0,4-1V) und Schaltverluste

## 1.5 Anwendungen

DC-DC-Wandler haben eine geringere Verlustleistung haben als Spannungsregler. Der mittlere Eingangsstrom ist – im Gegensatz zu Längsreglern – geringer als der Ausgangsstrom.

3

Beispiele:

- Bereitstellen von kleineren Spannungen (z.B. 12V, 5V) aus Industriespannungen (z.B. 24V)
- Bereitstellen der Prozessorversorgung
- Ladegeräte für Akkumulatoren (Sekundärbatterie)
- Stromquelle für Halbleiterlaser
- Drehzahlregelung bei Gleichstrommotoren
- Regelung von Peltierelementen (elektrothermischer Wandler)
- LED-Stromquellen

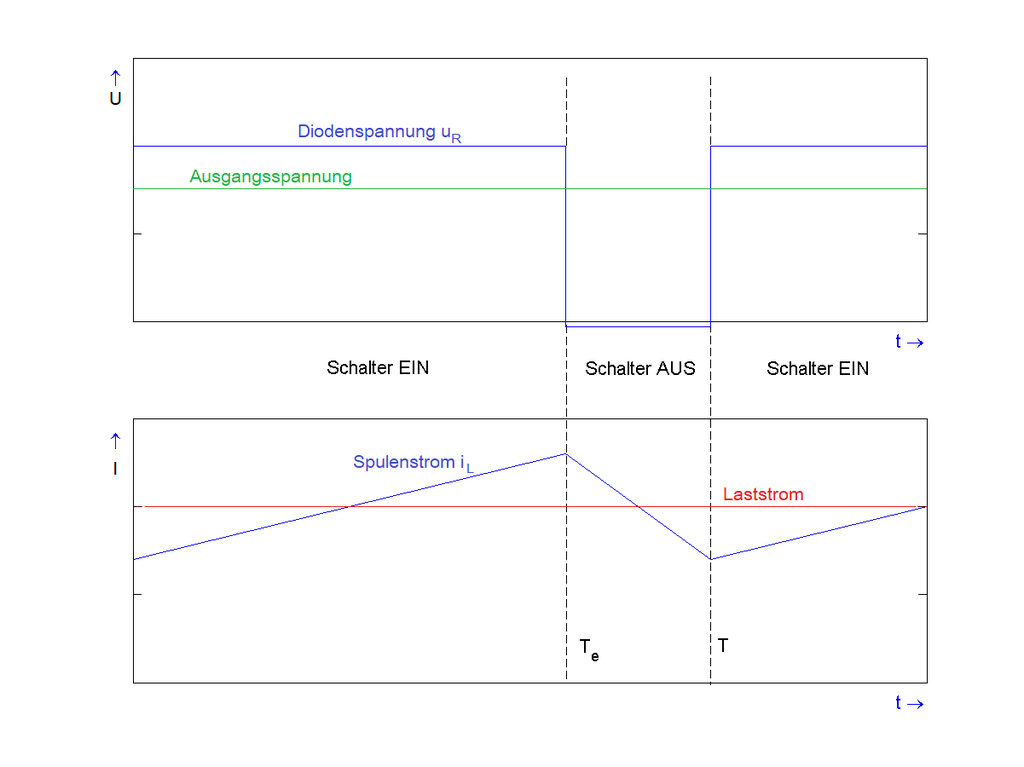
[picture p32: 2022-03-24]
Diplomarbeit/Steven Dudek/Informationen/Bilder/StepDown/DiodenspannungzuSpulenstrom.png

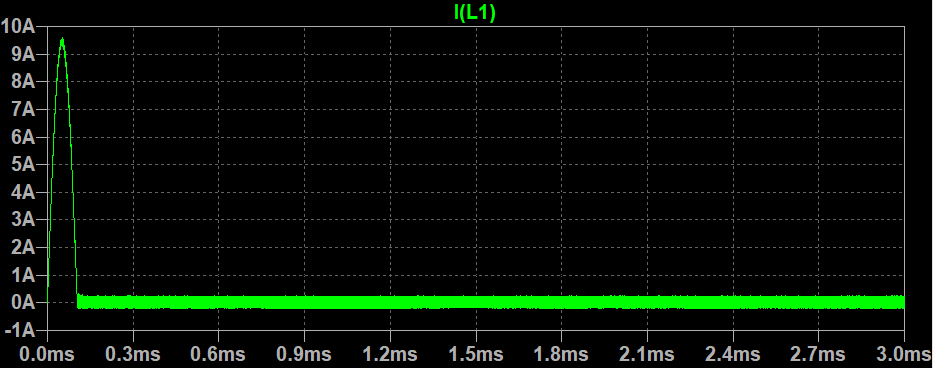
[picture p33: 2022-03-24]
Diplomarbeit/Steven Dudek/Informationen/Bilder/StepDown/lückenderBetrieb.PNG

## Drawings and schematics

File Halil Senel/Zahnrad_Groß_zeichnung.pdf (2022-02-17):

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

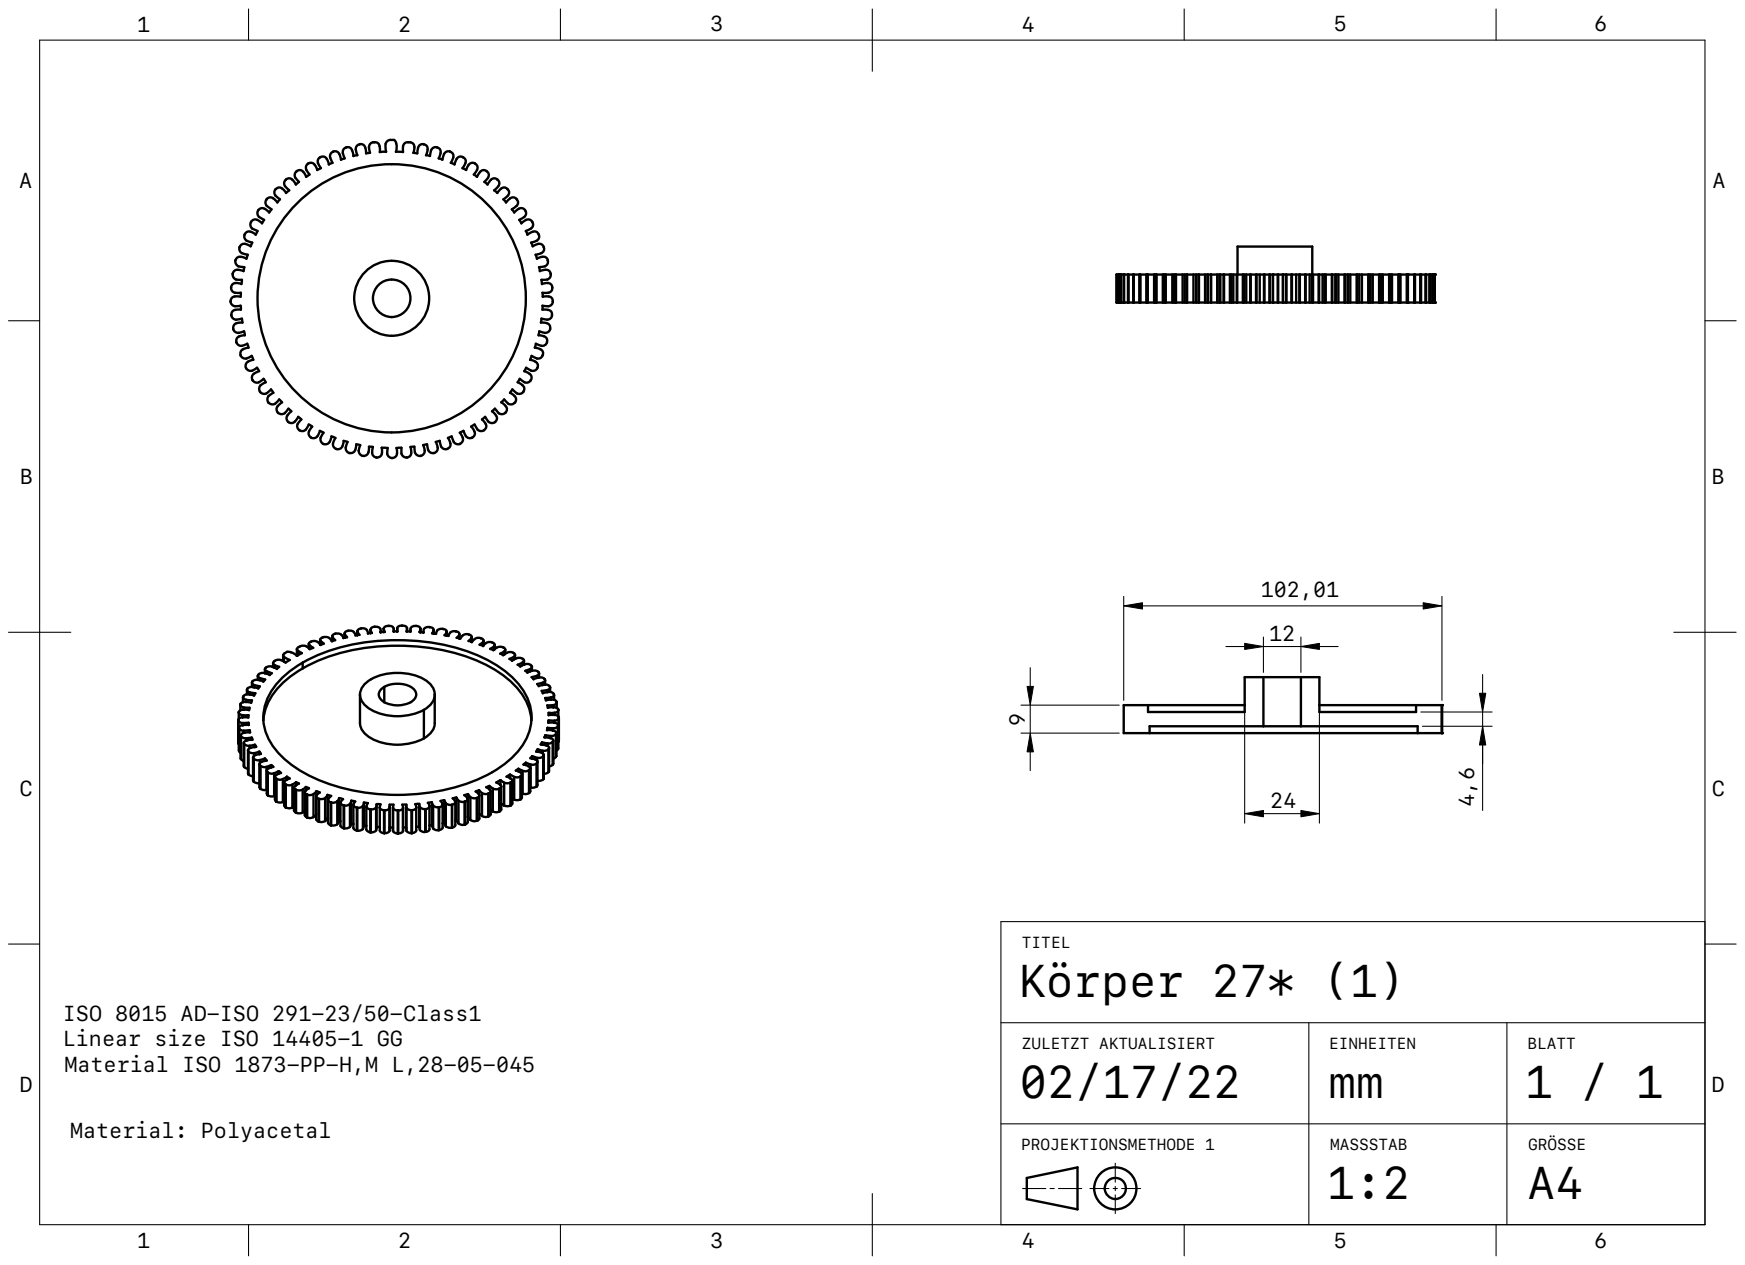
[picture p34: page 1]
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

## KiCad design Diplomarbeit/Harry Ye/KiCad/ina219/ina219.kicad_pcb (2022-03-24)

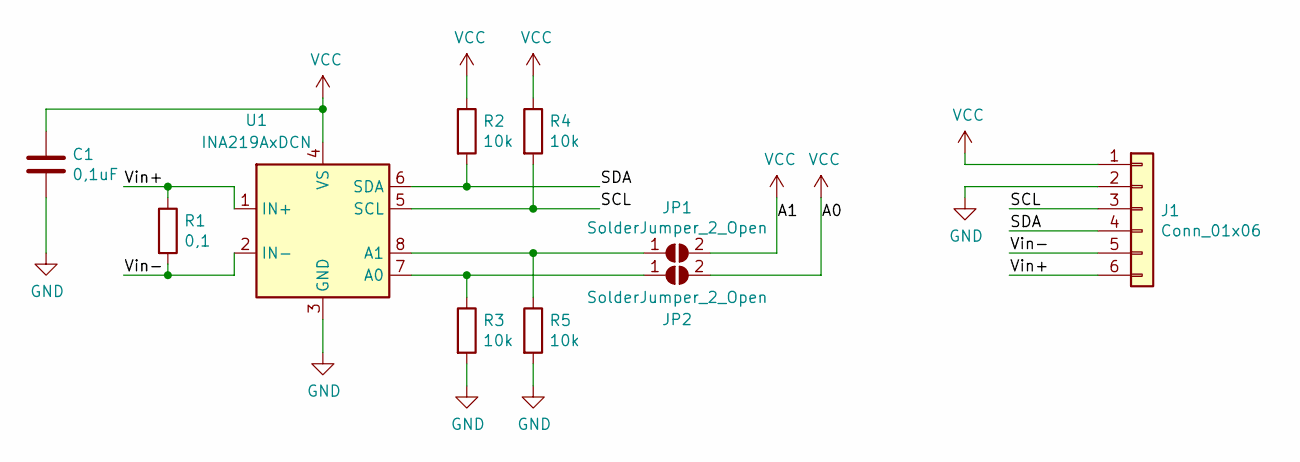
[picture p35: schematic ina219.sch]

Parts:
C1: 0,1uF; C_1206_3216Metric
J1: Conn_01x06; JST_EH_B6B-EH-A_1x06_P2.50mm_Vertical
JP1, JP2: SolderJumper_2_Open; SolderJumper-2_P1.3mm_Open_Pad1.0x1.5mm
R1: 0,1; R_2512_6332Metric
R2, R3, R4, R5: 10k; R_1206_3216Metric
U1: INA219AxDCN; SOT-23-8

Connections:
/SCL: J1.3, R4.2, U1.5 (SCL)
/SDA: J1.4, R2.2, U1.6 (SDA)
/Vin+: J1.6, R1.1, U1.1 (IN+)
/Vin-: J1.5, R1.2, U1.2 (IN-)
GND: C1.2, J1.2, R3.2, R5.2, U1.3 (GND)
unnamed: JP1.1 (A), R5.1, U1.8 (A1)
unnamed: JP2.1 (A), R3.1, U1.7 (A0)
VCC: C1.1, J1.1, JP1.2 (B), JP2.2 (B), R2.1, R4.1, U1.4 (VS)

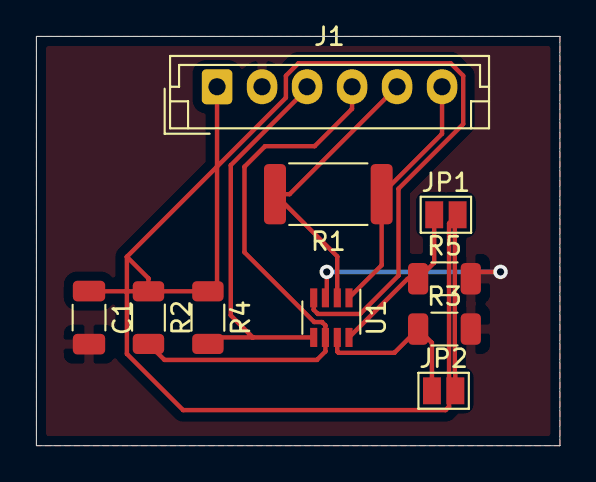
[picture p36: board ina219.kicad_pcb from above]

Board: 2 copper layers, 29.1 x 22.7 mm, 10 parts (0 on the bottom side), 8 nets.

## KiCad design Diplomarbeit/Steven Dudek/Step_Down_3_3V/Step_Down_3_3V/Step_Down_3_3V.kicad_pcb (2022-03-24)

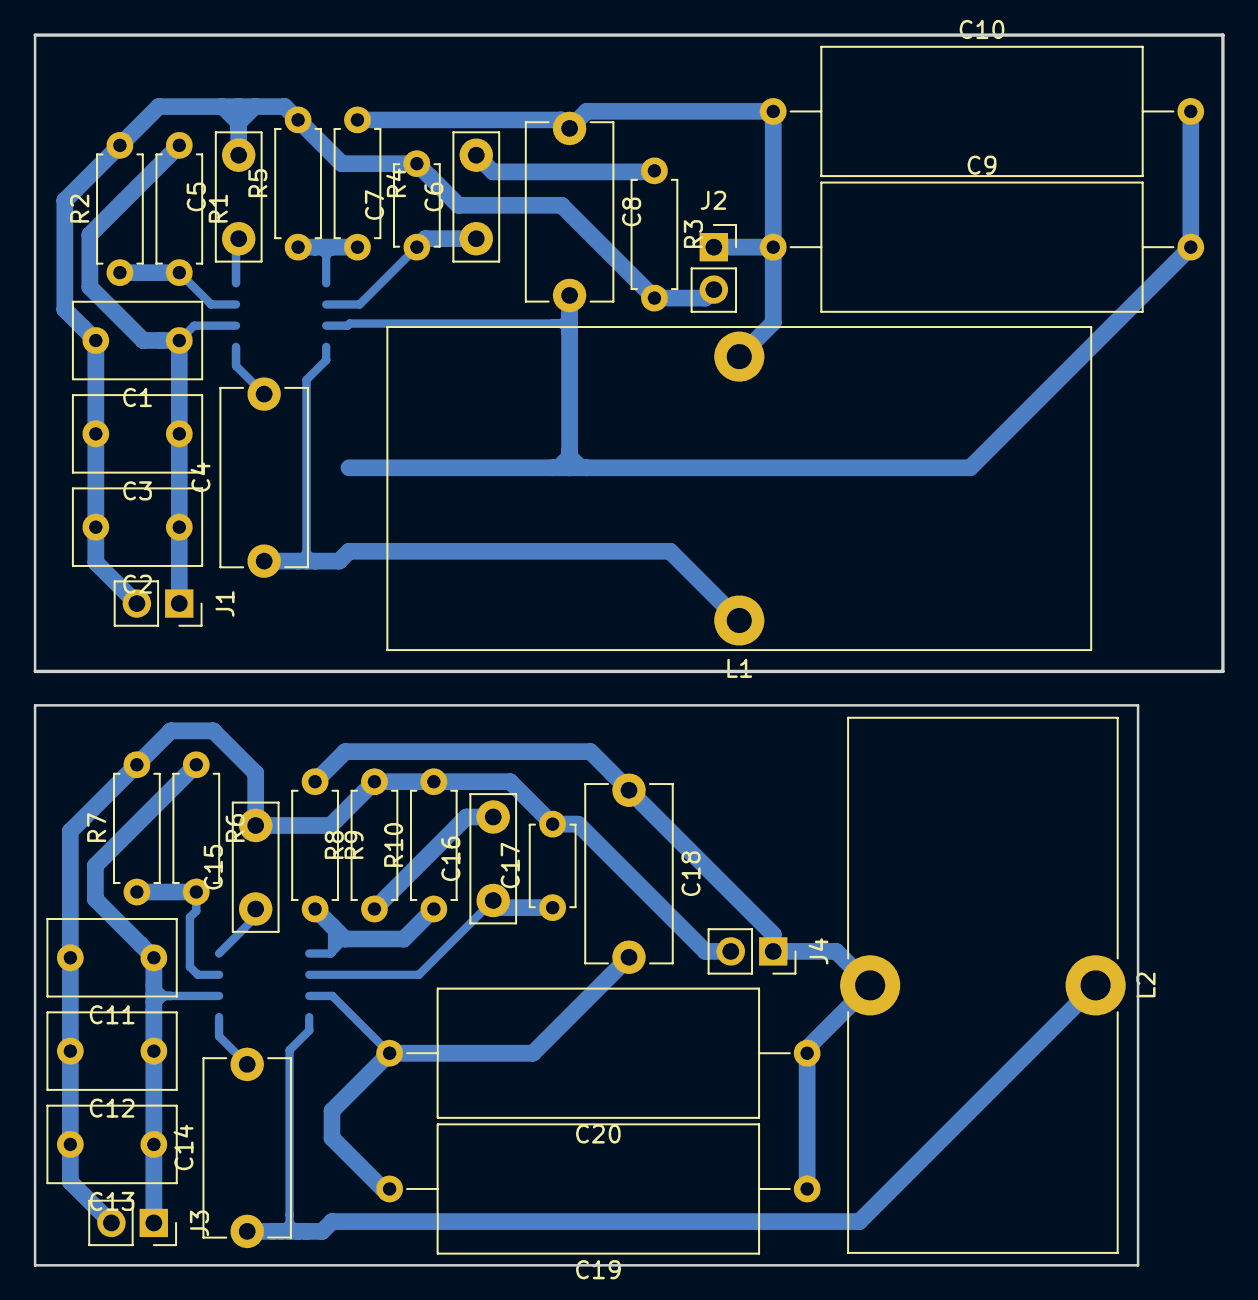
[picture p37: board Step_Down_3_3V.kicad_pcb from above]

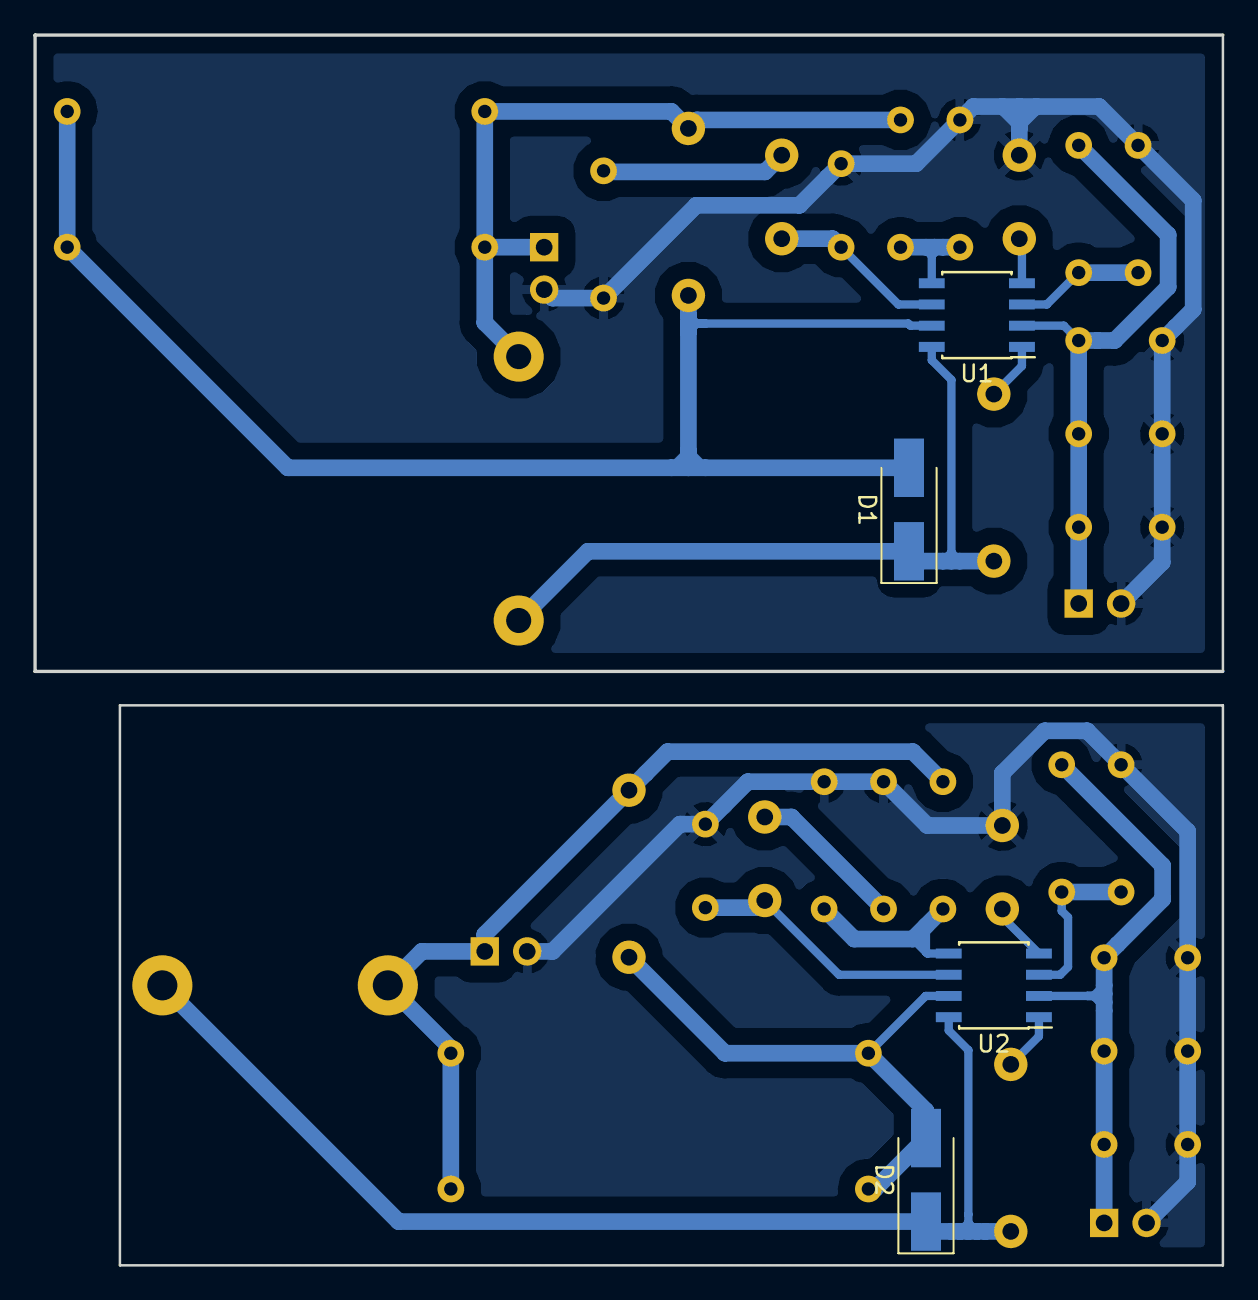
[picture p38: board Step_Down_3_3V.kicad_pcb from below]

Board: 2 copper layers, 71.1 x 73.7 mm, 40 parts (4 on the bottom side), 21 nets.

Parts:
C1, C2, C3, C11, C12, C13: 4.7µF; C_Disc_D7.5mm_W4.4mm_P5.00mm
C4, C8, C14, C18: 0.1µF; C_Disc_D10.5mm_W5.0mm_P10.00mm
C5, C15: 0.01µF; C_Disc_D7.5mm_W2.5mm_P5.00mm
C6, C16: 1000pF; C_Disc_D7.5mm_W2.5mm_P5.00mm
C7, C17: 47pF; C_Disc_D4.7mm_W2.5mm_P5.00mm
C9, C10, C19, C20: 47µF; C_Axial_L19.0mm_D7.5mm_P25.00mm_Horizontal
D1, D2: B340A; D_SMA_Handsoldering
J1, J2, J3, J4: Conn_01x02_Female; PinSocket_1x02_P2.54mm_Vertical
L1: 22µH; L_Toroid_Vertical_L41.9mm_W19.1mm_P15.80mm_Vishay_TJ7
L2: 12µH; L_Toroid_Vertical_L31.8mm_W15.9mm_P13.50mm_Bourns_5700
R1, R6: 332k; R_Axial_DIN0207_L6.3mm_D2.5mm_P7.62mm_Horizontal
R2, R7: 68.1k; R_Axial_DIN0207_L6.3mm_D2.5mm_P7.62mm_Horizontal
R3, R8: 29.4k; R_Axial_DIN0207_L6.3mm_D2.5mm_P7.62mm_Horizontal
R4, R9: 10.2k; R_Axial_DIN0207_L6.3mm_D2.5mm_P7.62mm_Horizontal
R5, R10: 3.24k; R_Axial_DIN0207_L6.3mm_D2.5mm_P7.62mm_Horizontal
U1, U2: TPS54331; SOIC-8_3.9x4.9mm_P1.27mm

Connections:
GND: C1.2, C2.2, C3.2, C5.2, C7.2, C11.2, C12.2, C13.2, C15.2, C17.2, J1.2, J2.2, J3.2, J4.2, R2.2, R3.2, R5.2, R7.2, R8.2, R10.2
unnamed: C1.1, C2.1, C3.1, J1.1, R1.1, U1.2
unnamed: C4.1, D1.1, L1.1, U1.8
unnamed: C4.2, U1.1
unnamed: C5.1, U1.4
unnamed: C6.1, C7.1, U1.6
unnamed: C6.2, R3.1
unnamed: C8.1, C9.1, C10.1, J2.1, L1.2, R4.1
unnamed: C8.2, C9.2, C10.2, D1.2, U1.7
unnamed: C11.1, C12.1, C13.1, J3.1, R6.1, U2.2
unnamed: C14.1, D2.1, L2.1, U2.8
unnamed: C14.2, U2.1
unnamed: C15.1, U2.4
unnamed: C16.1, C17.1, U2.6
unnamed: C16.2, R8.1
unnamed: C18.1, C19.1, C20.1, J4.1, L2.2, R9.1
unnamed: C18.2, C19.2, C20.2, D2.2, U2.7
unnamed: R1.2, R2.1, U1.3
unnamed: R4.2, R5.1, U1.5
unnamed: R6.2, R7.1, U2.3
unnamed: R9.2, R10.1, U2.5

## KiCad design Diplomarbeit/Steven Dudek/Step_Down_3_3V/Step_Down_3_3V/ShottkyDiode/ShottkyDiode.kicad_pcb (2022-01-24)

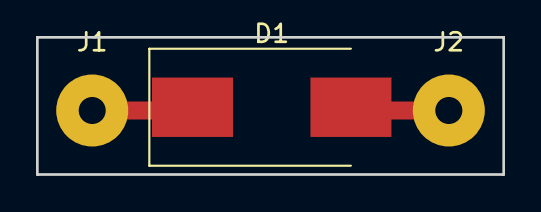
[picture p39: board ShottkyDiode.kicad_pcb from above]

Board: 2 copper layers, 25.9 x 7.6 mm, 3 parts (0 on the bottom side), 2 nets.

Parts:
D1: B340; D_SMC_Handsoldering
J1, J2: Conn_01x01_Male; SolderWirePad_1x01_Drill1.5mm

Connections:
unnamed: D1.1, J1.1
unnamed: D1.2, J2.1

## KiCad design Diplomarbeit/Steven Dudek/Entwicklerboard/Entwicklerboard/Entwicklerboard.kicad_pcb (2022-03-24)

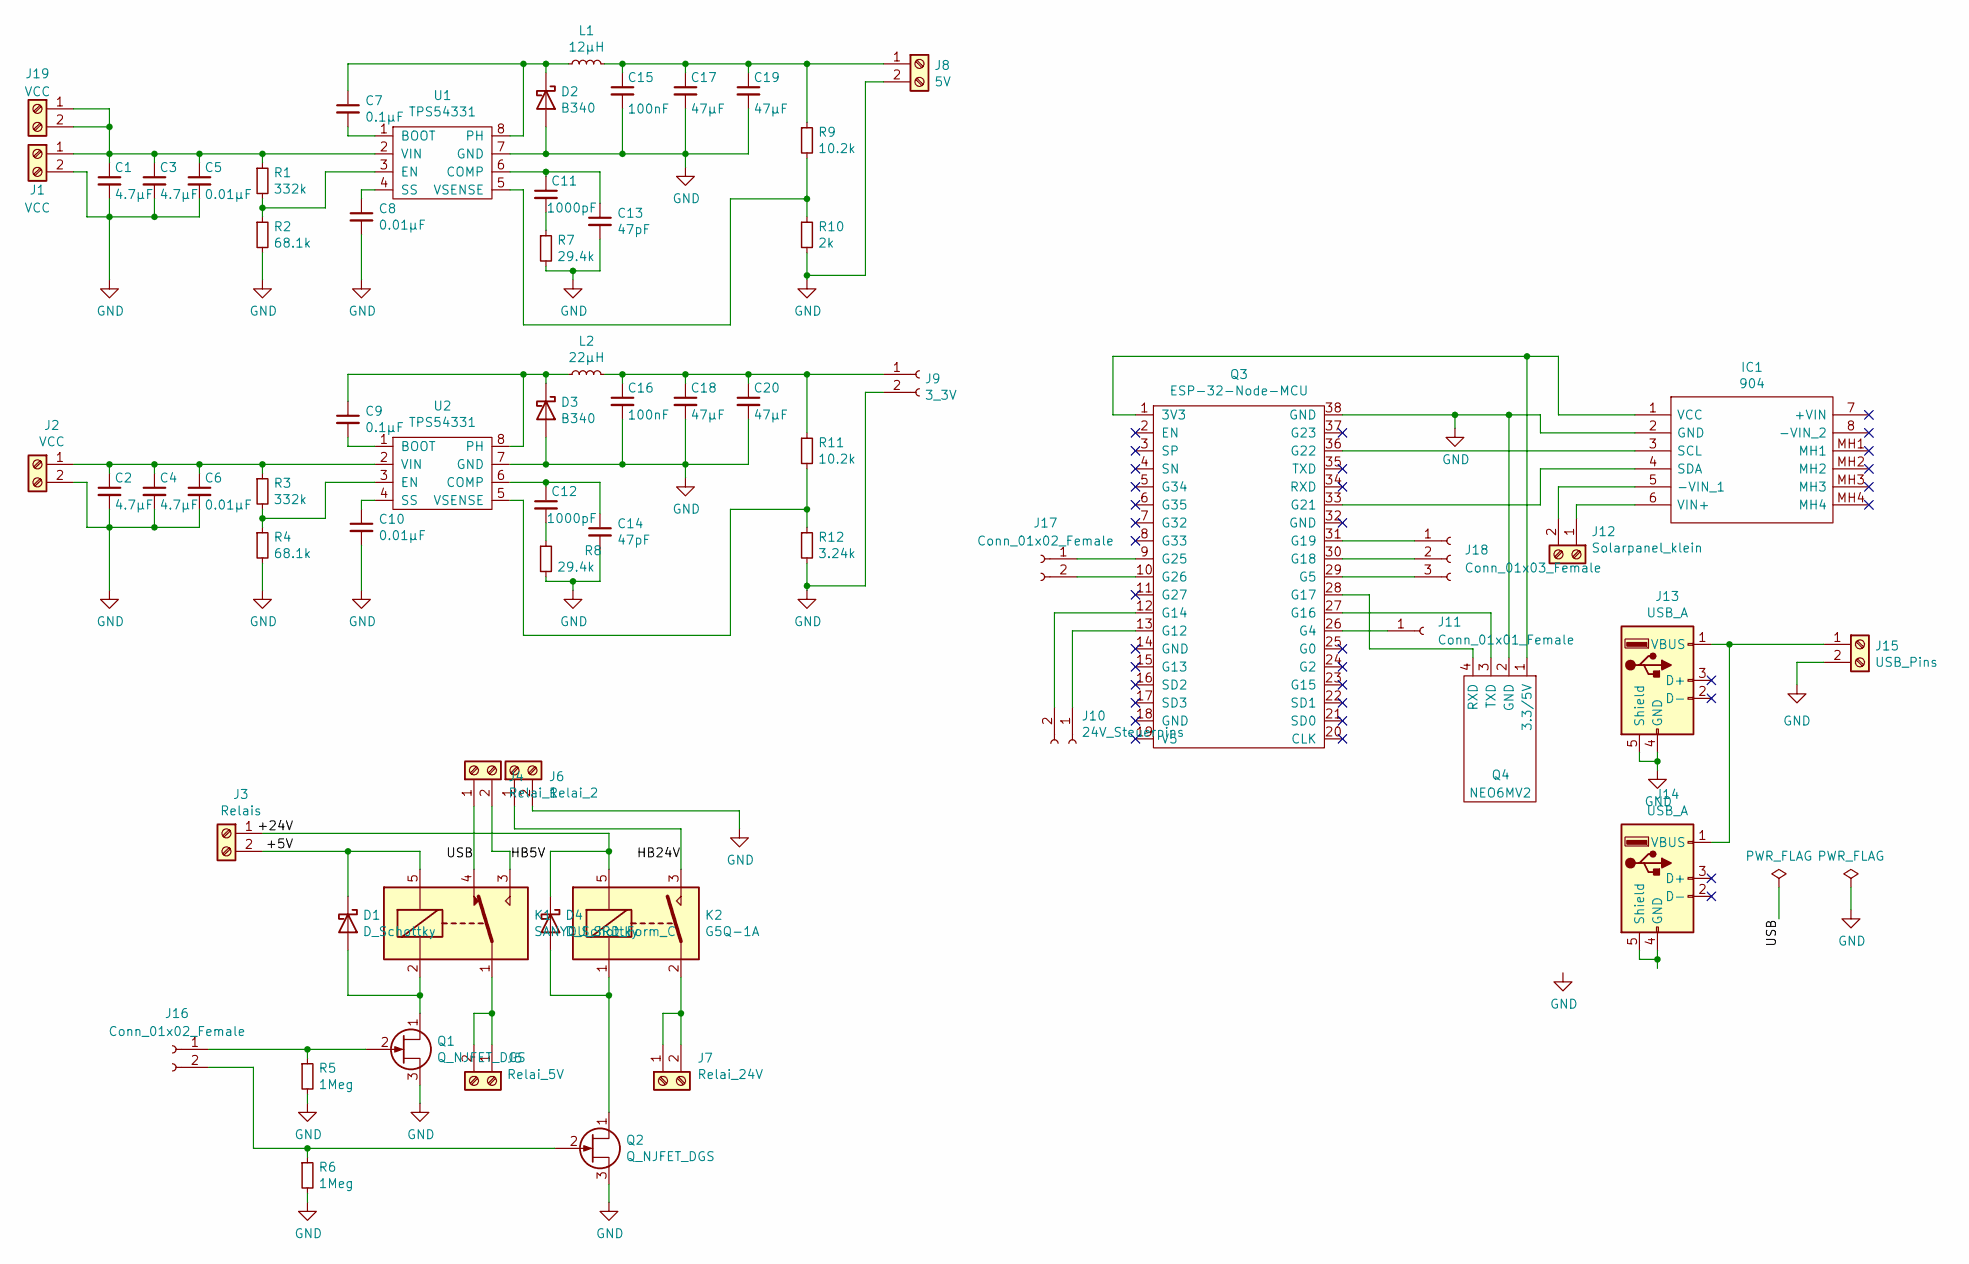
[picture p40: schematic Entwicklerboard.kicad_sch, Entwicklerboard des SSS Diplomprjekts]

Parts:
C1, C2, C3, C4: 4.7µF; C_1210_3225Metric_Pad1.42x2.65mm_HandSolder
C5, C6, C8, C10: 0.01µF; C_1206_3216Metric_Pad1.42x1.75mm_HandSolder
C7, C9: 0.1µF; C_1206_3216Metric_Pad1.42x1.75mm_HandSolder
C11, C12: 1000pF; C_1206_3216Metric_Pad1.42x1.75mm_HandSolder
C13, C14: 47pF; C_1206_3216Metric_Pad1.42x1.75mm_HandSolder
C15, C16: 100nF; C_1206_3216Metric_Pad1.42x1.75mm_HandSolder
C17, C18, C19, C20: 47µF; EEETC1V470P
D1, D4: D_Schottky; D_SMB_Handsoldering
D2, D3: B340; D_SMC
IC1: 904; Manufacturer_Part_Number 904
J1, J2, J19: VCC; TerminalBlock_Phoenix_MKDS-1,5-2-5.08_1x02_P5.08mm_Horizont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
J3: Relais; TerminalBlock_Phoenix_MKDS-1,5-2-5.08_1x02_P5.08mm_Horizont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
J4: Relai_1; TerminalBlock_Phoenix_MKDS-1,5-2-5.08_1x02_P5.08mm_Horizont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
J5: Relai_5V; TerminalBlock_Phoenix_MKDS-1,5-2-5.08_1x02_P5.08mm_Horizont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
J6: Relai_2; TerminalBlock_Phoenix_MKDS-1,5-2-5.08_1x02_P5.08mm_Horizont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
J7: Relai_24V; TerminalBlock_Phoenix_MKDS-1,5-2-5.08_1x02_P5.08mm_Horizont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
J8: 5V; TerminalBlock_Phoenix_MKDS-1,5-2-5.08_1x02_P5.08mm_Horizont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
J9: 3_3V; PinSocket_1x02_P2.54mm_Vertical
J10: 24V_Steuerpins; PinSocket_1x02_P2.54mm_Vertical
J11: Conn_01x01_Female; PinSocket_1x01_P2.54mm_Vertical
J12: Solarpanel_klein; TerminalBlock_Phoenix_MKDS-1,5-2-5.08_1x02_P5.08mm_Horizont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
J13, J14: USB_A; USB_A_CNCTech_1001-011-01101_Horizontal
J15: USB_Pins; TerminalBlock_Phoenix_MKDS-1,5-2-5.08_1x02_P5.08mm_Horizont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
J16, J17: Conn_01x02_Female; PinSocket_1x02_P2.54mm_Vertical
J18: Conn_01x03_Female; PinSocket_1x03_P2.54mm_Vertical
K1: SANYOU_SRD_Form_C; Relay_SPDT_SANYOU_SRD_Series_Form_C
K2: G5Q-1A; Relay_SPST_Omron-G5Q-1A
L1: 12µH; L_Toroid_Vertical_L31.8mm_W15.9mm_P13.50mm_Bourns_5700
L2: 22µH; L_Toroid_Vertical_L41.9mm_W19.1mm_P15.80mm_Vishay_TJ7
Q1, Q2: Q_NJFET_DGS; TO-220-3_Vertical
Q3: ESP-32-Node-MCU; ESP32-NodeMCU
Q4: NEO6MV2; GY-NEO6MV2
R1, R3: 332k; R_1206_3216Metric_Pad1.42x1.75mm_HandSolder
R2, R4: 68.1k; R_1206_3216Metric_Pad1.42x1.75mm_HandSolder
R5, R6: 1Meg; R_MiniMELF_MMA-0204
R7, R8: 29.4k; R_0805_2012Metric_Pad1.15x1.40mm_HandSolder
R9, R11: 10.2k; R_MiniMELF_MMA-0204
R10: 2k; R_1206_3216Metric_Pad1.42x1.75mm_HandSolder
R12: 3.24k; R_1206_3216Metric_Pad1.42x1.75mm_HandSolder
U1, U2: TPS54331; NE555DR

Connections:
/+5V: D1.1 (K), J3.2, K1.5
/+24V: D4.1 (K), J3.1, K2.5
/HB5V: J4.2, K1.3
/HB24V: J6.1, K2.3
/USB: J4.1, K1.4
unnamed: C1.1, C3.1, C5.1, J1.1, J19.1, J19.2, R1.1, U1.2 (VIN)
unnamed: C2.1, C4.1, C6.1, J2.1, R3.1, U2.2 (VIN)
unnamed: C7.1, D2.1 (K), L1.1, U1.8 (PH)
unnamed: C7.2, U1.1 (BOOT)
unnamed: C8.1, U1.4 (SS)
unnamed: C9.1, D3.1 (K), L2.1, U2.8 (PH)
unnamed: C9.2, U2.1 (BOOT)
unnamed: C10.1, U2.4 (SS)
unnamed: C11.1, C13.1, U1.6 (COMP)
unnamed: C11.2, R7.1
unnamed: C12.1, C14.1, U2.6 (COMP)
unnamed: C12.2, R8.1
unnamed: C15.1, C17.1, C19.1, J8.1, L1.2, R9.1
unnamed: C16.1, C18.1, C20.1, J9.1, L2.2, R11.1
unnamed: D1.2 (A), K1.2, Q1.1 (D)
unnamed: D4.2 (A), K2.1, Q2.1 (D)
unnamed: IC1.1 (VCC), Q3.1 (3V3), Q4.1 (3.3/5V)
unnamed: IC1.3 (SCL), Q3.36 (G22)
unnamed: IC1.4 (SDA), Q3.33 (G21)
unnamed: IC1.5 (-VIN_1), J12.2
unnamed: IC1.6 (VIN+), J12.1
unnamed: J5.1, J5.2, K1.1
unnamed: J7.1, J7.2, K2.2
unnamed: J10.1, Q3.13 (G12)
unnamed: J10.2, Q3.12 (G14)
unnamed: J11.1, Q3.26 (G4)
unnamed: J13.1 (VBUS), J14.1 (VBUS), J15.1
unnamed: J16.1, Q1.2 (G), R5.1
unnamed: J16.2, Q2.2 (G), R6.1
unnamed: J17.1, Q3.9 (G25)
unnamed: J17.2, Q3.10 (G26)
unnamed: J18.1, Q3.31 (G19)
unnamed: J18.2, Q3.30 (G18)
unnamed: J18.3, Q3.29 (G5)
unnamed: Q3.27 (G16), Q4.3 (TXD)
unnamed: Q3.28 (G17), Q4.4 (RXD)
unnamed: R1.2, R2.1, U1.3 (EN)
unnamed: R3.2, R4.1, U2.3 (EN)
unnamed: R9.2, R10.1, U1.5 (VSENSE)
unnamed: R11.2, R12.1, U2.5 (VSENSE)

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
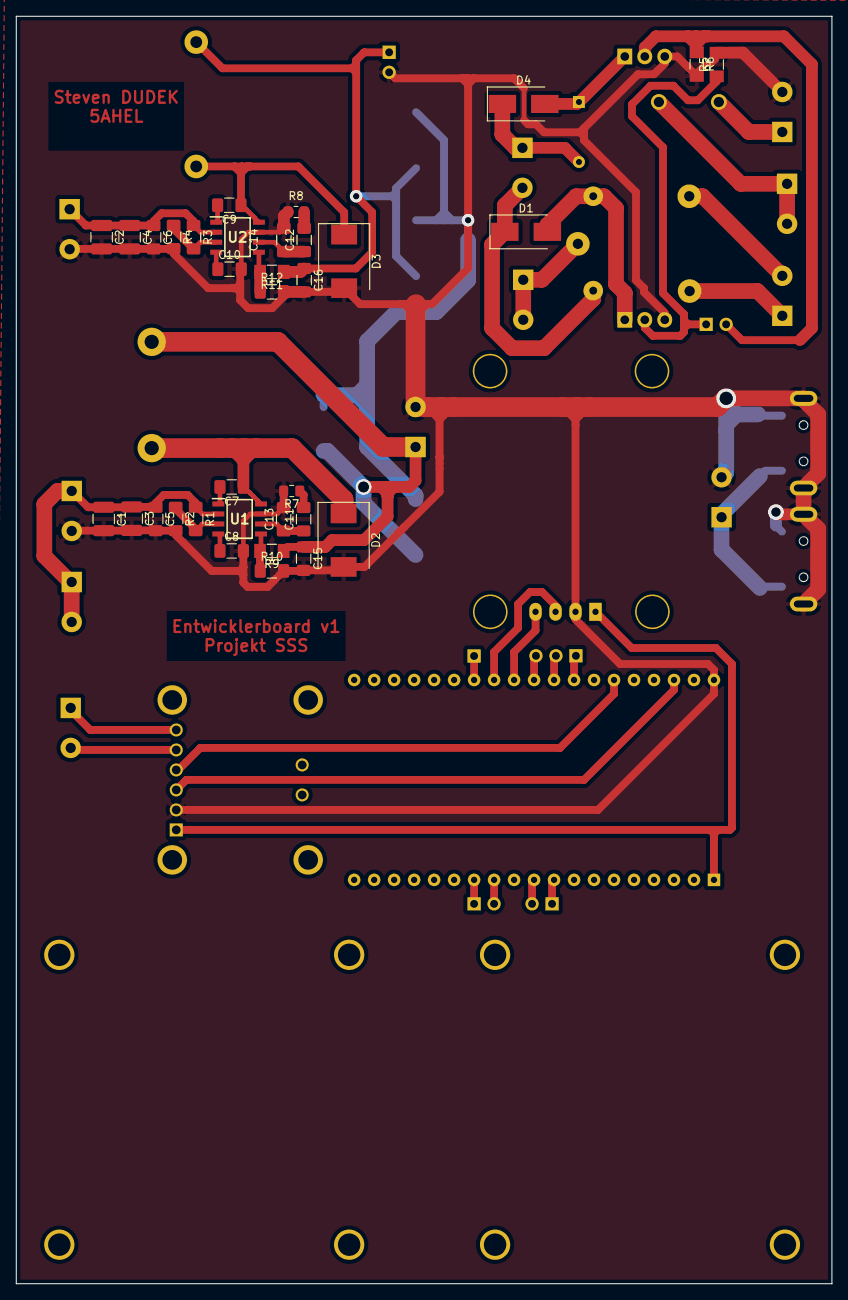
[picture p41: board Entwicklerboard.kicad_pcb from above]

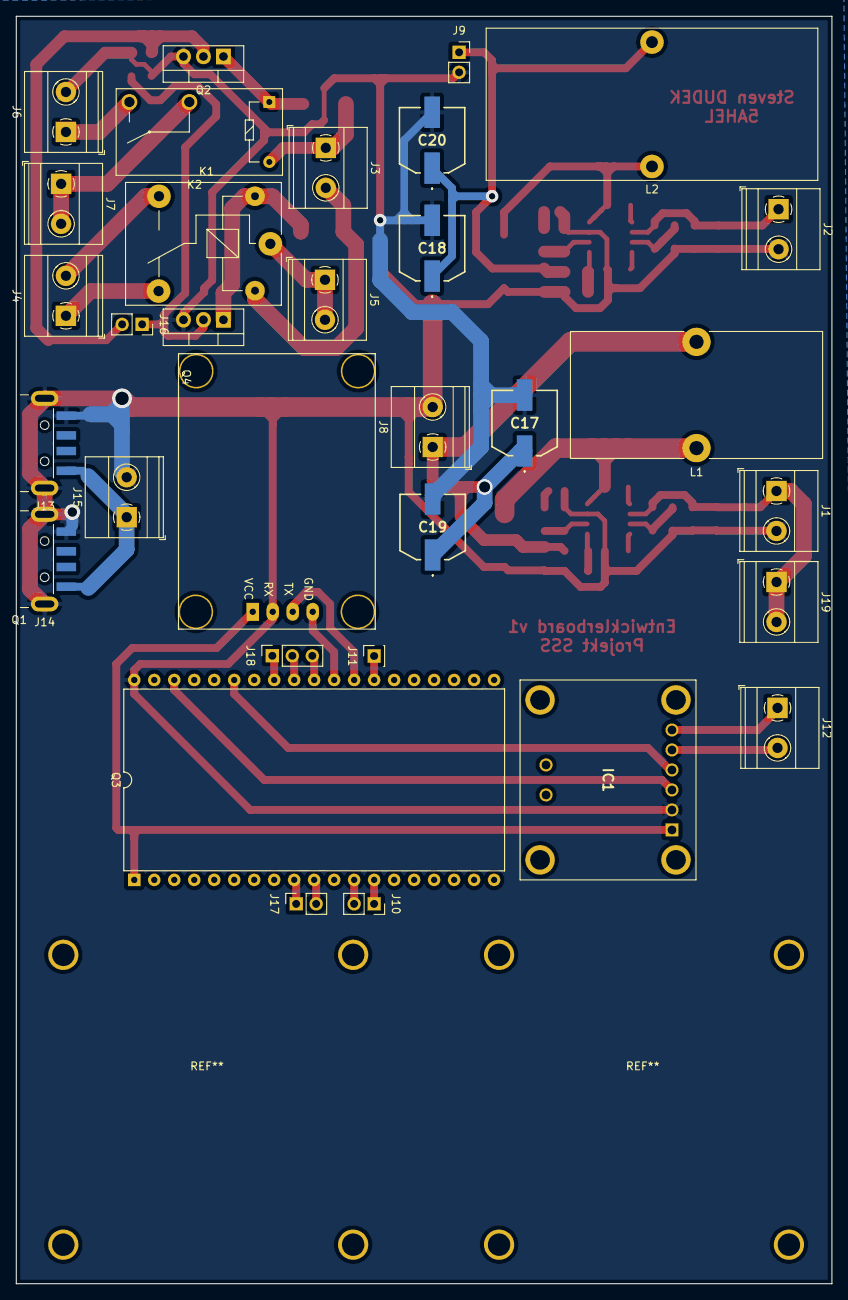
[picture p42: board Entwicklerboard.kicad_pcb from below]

Board: 2 copper layers, 103.6 x 161.0 mm, 66 parts (32 on the bottom side), 46 nets.

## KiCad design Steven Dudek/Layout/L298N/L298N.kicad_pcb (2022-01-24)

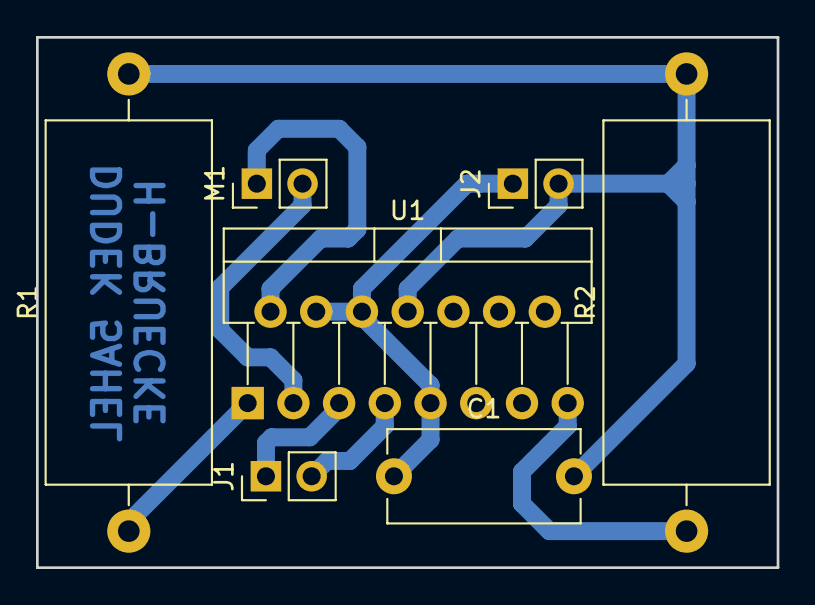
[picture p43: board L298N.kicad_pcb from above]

Board: 2 copper layers, 41.1 x 29.5 mm, 7 parts (0 on the bottom side), 8 nets.

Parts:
C1: 100nF; C_Disc_D10.5mm_W5.0mm_P10.00mm
J1, J2: Conn_01x02_Female; PinHeader_1x02_P2.54mm_Vertical
M1: Motor_DC; PinHeader_1x02_P2.54mm_Vertical
R1, R2: 1; R_Axial_DIN0922_L20.0mm_D9.0mm_P25.40mm_Horizontal
U1: L298HN; TO-220-15_P2.54x2.54mm_StaggerOdd_Lead4.58mm_Vertical

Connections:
+5V: C1.1, J2.1, U1.4, U1.6, U1.9
/ESP_IN1: J1.1, U1.5
/ESP_IN2: J1.2, U1.7
GND: C1.2, J2.2, R1.2, R2.2, U1.8
unnamed: M1.1, U1.2
unnamed: M1.2, U1.3
unnamed: R1.1, U1.1
unnamed: R2.1, U1.15

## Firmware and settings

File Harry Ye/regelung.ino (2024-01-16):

#include <Wire.h>
#include <INA219_WE.h>
#include <Stepper.h>
#define I2C_ADDRESS 0x40

/* There are several ways to create your INA219 object:
 * INA219_WE ina219 = INA219_WE()              -> uses Wire / I2C Address = 0x40
 * INA219_WE ina219 = INA219_WE(ICM20948_ADDR) -> uses Wire / I2C_ADDRESS
 * INA219_WE ina219 = INA219_WE(&wire2)        -> uses the TwoWire object wire2 / I2C_ADDRESS
 * INA219_WE ina219 = INA219_WE(&wire2, I2C_ADDRESS) -> all together
 * Successfully tested with two I2C busses on an ESP32
 */
INA219_WE ina219 = INA219_WE(I2C_ADDRESS);

const int stepsPerRevolution = 200;
Stepper myStepper(stepsPerRevolution, 8, 9, 10, 11);

const int lin1 = 7;
const int lin2 = 6;
const int linpwm = 5;

void setup() {
  Serial.begin(9600);
  Wire.begin();
  if(!ina219.init()){
    Serial.println("INA219 not connected!");
  }

  /* Set ADC Mode for Bus and ShuntVoltage
  * Mode *            * Res / Samples *       * Conversion Time *
  BIT_MODE_9        9 Bit Resolution             84 µs
  BIT_MODE_10       10 Bit Resolution            148 µs  
  BIT_MODE_11       11 Bit Resolution            276 µs
  BIT_MODE_12       12 Bit Resolution            532 µs  (DEFAULT)
  SAMPLE_MODE_2     Mean Value 2 samples         1,06 ms
  SAMPLE_MODE_4     Mean Value 4 samples         2,13 ms
  SAMPLE_MODE_8     Mean Value 8 samples         4,26 ms
  SAMPLE_MODE_16    Mean Value 16 samples        8,51 ms     
  SAMPLE_MODE_32    Mean Value 32 samples        17,02 ms
  SAMPLE_MODE_64    Mean Value 64 samples        34,05 ms
  SAMPLE_MODE_128   Mean Value 128 samples       68,10 ms
  */
  ina219.setADCMode(SAMPLE_MODE_128); // choose mode and uncomment for change of default
  
  /* Set measure mode
  POWER_DOWN - INA219 switched off
  TRIGGERED  - measurement on demand
  ADC_OFF    - Analog/Digital Converter switched off
  CONTINUOUS  - Continuous measurements (DEFAULT)
  */
  ina219.setMeasureMode(CONTINUOUS); // choose mode and uncomment for change of default
  
  /* Set PGain
  * Gain *  * Shunt Voltage Range *   * Max Current *
   PG_40       40 mV                    0,4 A
   PG_80       80 mV                    0,8 A
   PG_160      160 mV                   1,6 A
   PG_320      320 mV                   3,2 A (DEFAULT)
  */
  ina219.setPGain(PG_40); // choose gain and uncomment for change of default
  
  /* Set Bus Voltage Range
   BRNG_16   -> 16 V
   BRNG_32   -> 32 V (DEFAULT)
  */
  ina219.setBusRange(BRNG_16); // choose range and uncomment for change of default

  Serial.println("INA219 Current Sensor Example Sketch - Continuous");

  /* If the current values delivered by the INA219 differ by a constant factor
     from values obtained with calibrated equipment you can define a correction factor.
     Correction factor = current delivered from calibrated equipment / current delivered by INA219
  */
  // ina219.setCorrectionFactor(0.98); // insert your correction factor if necessary
  myStepper.setSpeed(5);
  
  pinMode(lin1, OUTPUT);
  pinMode(lin2, OUTPUT);
  pinMode(linpwm, OUTPUT);
}

int upflag = 0;
int downflag = 0;

int current_position = 0;
int highest_position = 0;
int diff_position = 0;
int linflag = 0;
float oldcurrent_mA = 0.0;
float avrcurrent_mA = 0.0;
float shuntVoltage_mV = 0.0;
float loadVoltage_V = 0.0;
float busVoltage_V = 0.0;
float current_mA = 0.0;
float power_mW = 0.0; 
float highestcurrent_mA = 0.0;
bool ina219_overflow = false;
float tolerance1 = 10;
float tolerance2 = 10;

void loop() {
  current_mA = 0.0;
  avrcurrent_mA = 0.0;
  oldcurrent_mA = 0.0;
  digitalWrite(lin1, LOW);
  digitalWrite(lin2, LOW);
  
  shuntVoltage_mV = ina219.getShuntVoltage_mV();
  current_mA = ina219.getCurrent_mA();
  power_mW = ina219.getBusPower();
  loadVoltage_V  = busVoltage_V + (shuntVoltage_mV/1000);
  ina219_overflow = ina219.getOverflow();
  
  Serial.print("Shunt Voltage [mV]: "); Serial.println(shuntVoltage_mV);
  Serial.print("Bus Voltage [V]: "); Serial.println(busVoltage_V);
  Serial.print("Load Voltage [V]: "); Serial.println(loadVoltage_V);
  Serial.print("Current[mA]: "); Serial.println(current_mA);
  if(!ina219_overflow){
    Serial.println("Values OK - no overflow");
  }
  else{
    Serial.println("Overflow! Choose higher PGAIN");
  }
  Serial.println();
  
  delay(1000);
  /*
  for(int i=0; i<10; i++){
    current_mA = ina219.getCurrent_mA();
    avrcurrent_mA += current_mA;
    avrcurrent_mA /= i;
  }
  */
  /*
  switch(Time){
    case 8:                 //8 Uhr
      maxcurrent_mA = 80;
      break;
    case 9:                 //9 Uhr
      maxcurrent_mA = 170;
      break;
    case 10:                //10 Uhr
      maxcurrent_mA = 220;
      break;
    case 11:                //11 Uhr
      maxcurrent_mA = 240;
      break;
    case 12:                //12 Uhr
      maxcurrent_mA = 270;
      break;
    case 13:                //13 Uhr
      maxcurrent_mA = 240;
      break;
    case 14:                //14 Uhr
      maxcurrent_mA = 220;
      break;
    case 15:                //15 Uhr
      maxcurrent_mA = 170;
      break;
    case 16:                //16 Uhr
      maxcurrent_mA = 80;
      break;
    default:                //keine gerade Uhrzahl
      maxcurrent_mA = 1000;
      break;
  }
  */
  while(current_position <= 360){                                         //Wird wiederholt so lange bis mehr als 360 Schritte zurückgelegt wurden
    current_mA = ina219.getCurrent_mA();                                  //Strom messen
    Serial.print("Current[mA]: "); Serial.println(current_mA);            //Strom ausgeben
    Serial.println("clockwise");                                          //Motor in Uhrzeigersinn
    myStepper.step(1);                                                    //geht ein Schritt 
    current_position++;                                                   //jetzige Position inkrementiert
    Serial.println(current_position);                                     //Positionsausgabe
    if(oldcurrent_mA < current_mA){                                       //Wenn der jetzige Strom größer ist als der ältere Strom
      highestcurrent_mA = current_mA;                                     //Dann ist jetziger Strom der höchste
      highest_position = current_position;                                //jetzige Position wird gespeichert
    }
    if(oldcurrent_mA > (current_mA+tolerance1)){                          //Wenn der jetzige Strom kleiner ist als der ältere Strom mit Toleranz
      Serial.print("OLDCurrent[mA]: "); Serial.println(oldcurrent_mA);    //älterer Strom Ausgabe
      Serial.print("Current[mA]: "); Serial.println(current_mA);          //Jetziger Strom Ausgabe
      diff_position = current_position - highest_position;                //Differenz zwischen jetzige und bester Position
      Serial.println("counterclockwise");                                 //Schrittmotor dreht zurück
      myStepper.step(-(diff_position));                                   //Dreht sich zurück zur Höchststelle
      current_position -= diff_position;                                  //Jetzige Position ausrechnen
      Serial.println(current_position);                                   //Ausgeben
      linflag = 1;                                                        //Flag setzen
      break;                                                              //Aus der Schleife ausbrechen
    }
    oldcurrent_mA = current_mA;                                           //älterer Wert wird mit neuem ersetzt
  }
  
  oldcurrent_mA = 0;
                                            
  while(linflag == 1){                                                    //Wiederholt nur so lange flag 1
    if(current_position >= 180){                                          //unter 180 Schritte sein
      current_mA = ina219.getCurrent_mA();                                
      Serial.print("Current[mA]: "); Serial.println(current_mA);
      if(downflag == 0){                                                  //flag muss 0 sein
        Serial.println("down");
        digitalWrite(lin1, LOW);                                          //Motor einziehen
        digitalWrite(lin2, HIGH);
        analogWrite(linpwm, 100);                                         //Geschwindigkeit
        Serial.print("Current[mA]: "); Serial.println(current_mA);
        downflag = 1;
      }
      
      if(oldcurrent_mA > (current_mA+tolerance2)){                        //Wenn der jetzige Strom kleiner ist als der ältere Strom mit Toleranz
        Serial.print("OLDCurrent[mA]: "); Serial.println(oldcurrent_mA);
        Serial.print("Current[mA]: "); Serial.println(current_mA);
        Serial.println("up");
        digitalWrite(lin1, HIGH);                                         //Fährt wieder aus für eine kurze Zeit
        digitalWrite(lin2, LOW);
        delay(1000);
        digitalWrite(lin1, LOW);
        Serial.print("Current[mA]: "); Serial.println(current_mA);
        linflag = 0;
        downflag = 0;
        break;
      }
      
    oldcurrent_mA = current_mA;
    }
    else{
      current_mA = ina219.getCurrent_mA();
      Serial.print("Current[mA]: "); Serial.println(current_mA);
      if(upflag == 0){
        Serial.println("up");
        digitalWrite(lin1, HIGH);                                         //Motor fährt aus
        digitalWrite(lin2, LOW);
        analogWrite(linpwm, 100);
        Serial.print("Current[mA]: "); Serial.println(current_mA);
        upflag = 1;
      }
      if(oldcurrent_mA > (current_mA+tolerance2)){
        Serial.print("OLDCurrent[mA]: "); Serial.println(oldcurrent_mA);
        Serial.print("Current[mA]: "); Serial.println(current_mA);
        Serial.println("down");
        digitalWrite(lin1, LOW);                                          //Motor zieht sich für eine kurze Zeit ein
        digitalWrite(lin2, HIGH);
        delay(1000);
        digitalWrite(lin2, LOW);
        Serial.print("Current[mA]: "); Serial.println(current_mA);
        linflag = 0;
        upflag = 0;
        break;
      }
    oldcurrent_mA = current_mA;
    }
  }
  if(current_position >= 360){                                            //Nach 360 Schritte zurückdrehen
    Serial.println("counterclockwise");
    myStepper.step(-100);
    myStepper.step(-100);
  }
}

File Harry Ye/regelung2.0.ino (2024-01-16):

#include <Wire.h>
#include <INA219_WE.h>
#include <Stepper.h>
#define I2C_ADDRESS 0x40

INA219_WE ina219 = INA219_WE(I2C_ADDRESS);

const int stepsPerRevolution = 200;
Stepper motor(stepsPerRevolution, 8, 9, 10, 11);

const int lin1 = 7;
const int lin2 = 6;
const int pwm = 5;

float current = 0.0;
bool ina219_overflow = false;
int steps = 200;

void azimut(int schritte) {
  float highestcurrent = 0.0;                 //höchster Stromwert im Winkelbereich zwischen Süden und Westen
  int highestposition = 0;                    //Position vom höchsten Stromwert SW
  float highestcurrent1 = 0.0;                //höchster Stromwert im Winkelbereich zwischen Süden und Osten
  int highestposition1 = 0;                   //Position vom höchsten Stromwert SO
  for(int i=0;i<=schritte;i++) {              //for-Schleife wiederholt sich bis angebene Schrittanzahl erreicht wurde
    motor.step(1);                            //Schrittmotor bewegt sich einen Schritt Gegen-Uhrzeigersinn
    current = ina219.getCurrent_mA();         //Strom wird gemessen
    Serial.println(current);                  //Strom wird ausgegeben
    Serial.println(i);                        //jetzige Position ausgeben
    if(current > highestcurrent) {            //Wenn der jetzige Strom größer ist als der höchste Strom
      highestcurrent = current;               //Dann ist jetziger Strom der höchste
      highestposition = i;                    //jetzige Position wird gespeichert
      Serial.print("Current "); Serial.println(highestcurrent);
      Serial.print("Position "); Serial.println(highestposition);
    }
  }
  motor.step(-schritte);                      //Schrittmotor dreht sich zurück zum Nullpunkt
  for(int i=0;i<=schritte;i++) {              //for-Schleife wiederholt sich bis angebene Schrittanzahl erreicht wurde
    motor.step(-1);                           //Schrittmotor bewegt sich einen Schritt Uhrzeigersinn
    current = ina219.getCurrent_mA();         //Strom wird gemessen
    Serial.println(current);                  //Strom wird ausgegeben
    Serial.println(i);                        //jetzige Position ausgeben
    if(current > highestcurrent1) {           //Wenn der jetzige Strom größer ist als der höchste Strom
      highestcurrent1 = current;              //Dann ist jetziger Strom der höchste
      highestposition1 = i;                   //jetzige Position wird gespeichert
      Serial.print("Current "); Serial.println(highestcurrent1);        
      Serial.print("Position "); Serial.println(highestposition1); 
    }
  }
  motor.step(schritte);                       //Schrittmotor dreht sich zurück zum Nullpunkt
  if(highestcurrent > highestcurrent1) {      //Ist Stromwert SW größer als Stromwert SO
    motor.step(highestposition);              //Motor dreht sich zum Position vom Stromwert SW
    Serial.println(highestposition);          //höchste Position ausgeben
    current = ina219.getCurrent_mA();         //Strom wird gemessen
    Serial.println(current);                  //Strom wird ausgegeben
  }
  else if(highestcurrent < highestcurrent1){
    motor.step(-highestposition1);            //Ist Stromwert SO größer als Stromwert SW
    Serial.println(highestposition1);          //höchste Position ausgeben
    current = ina219.getCurrent_mA();         //Strom wird gemessen
    Serial.println(current);                  //Strom wird ausgegeben
  }
  else {
    Serial.println("Es ist bewölkt oder es gibt kein Licht");
  }
}

void elevation() {
  float highestcurrent = 0.0;                       //Höchster gemessener Strom
  int highestposition = 0;                          //Position des Höchststromes
  digitalWrite(lin1, HIGH);                         //Linearmotor fährt aus
  digitalWrite(lin2, LOW);                           
  analogWrite(pwm, 100);                            //PWM Pin 5 steuert die Geschwindigkeit des Linearmotors
  for(int i=0;i<=200;i++) {                         //for-Schleife wiederholt bis 200 erreicht wird
    current = ina219.getCurrent_mA();               //Strom wird gemessen
    Serial.println(current);                        //Strom wird ausgegeben
    if(current > highestcurrent){                   //Wenn der jetzige Strom größer ist als der höchste Strom
      highestcurrent = current;                     //Dann ist jetziger Strom der höchste
      Serial.print("Current "); Serial.println(highestcurrent);
      highestposition = (i*100);                    //jetzige Position wird gespeichert
      Serial.print("Position "); Serial.println(highestposition);
    }
    delay(100);                                     //Verzögerung von 100ms
  }
  digitalWrite(lin1, LOW);                          //Linearmotor zieht sich ein
  digitalWrite(lin2, HIGH);
  delay(35000);
  digitalWrite(lin1, HIGH);                         //Linearmotor fährt zur Position
  digitalWrite(lin2, LOW);
  delay(highestposition);
  digitalWrite(lin1, LOW);
}
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

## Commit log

2022-01-24 4th Upload
    [Stückliste.xlsx]
2022-01-25 Add files via upload
    Linearantrieb Motor testen
2022-01-25 Add files via upload
    Testcode für Motoransteuerung mit GPS-Daten
2022-03-24 24.03.2022 Upload
    [Stundenaufzeichnung.xlsx, Stückliste.xlsx]
2022-03-24 24.04.2022 Upload
    [Entwicklerboard.kicad_pcb, Entwicklerboard.kicad_sch, Entwicklerboard.sch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]
